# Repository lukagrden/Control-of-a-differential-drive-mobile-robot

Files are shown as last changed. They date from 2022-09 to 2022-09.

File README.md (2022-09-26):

# Upravljanjem mobilnim robotom na diferencijalni pogon - završni rad

## SAŽETAK

Završni rad opisuje modifikaciju mobilnog robota Pioneer 2DX koji koristi diferencijalni sustav pogona. Robot je nadograđen s novim upravljačkim i pogonskim komponentama uz koje je izrađen upravljački algoritam niske razine s mogućnošću dvosmjerne komunikacije s nadređenim upravljačkim računalima. U sklopu zadatka projektiran je regulator brzine vrtnje elektromotora čije su performanse ispitane odzivima na različite pobudne funkcije. Nadalje, primjenom jednadžbi direktne kinematike podređeni upravljački sustav vrši izračun referenci brzine vrtnje kotača u odnosu na željene translacijske i rotacijske brzine, dok se jednadžbama direktne kinematike tada preko enkodera estimiraju realne brzine robota. Serijska komunikacija s nadređenim računalom izvedena je pomoću robotskog operativnog sustava (eng. Robot Operating System – ROS) primjenom paketa „rosserial“. Dodatno, rad obuhvaća konstruiranje i izradu adaptera novih pogonskih motora tehnologijom 3D ispisa, uz koje je također prikazana shema spajanja upravljačkih komponenti te je izrađena prototipna pločica.

Sva dokumentacija koja se tiče upravljačkog programa s modoficiranim knjižnicama, nalazi se u završnom radu (Grden_2022_zavrsni_preddiplomski.pdf). Uz to na repozitoriju su dodane
step. datoteke modeliranih dijelovima zajedno s upravljačkim kodom mobilnog robota.

 

# Control of a differential drive mobile robot - final paper

## SUMMARY

The final paper describes the modification of the Pioneer 2DX mobile robot that uses a differential drive system. The robot was upgraded with new control and drive components, along with which a low-level control algorithm was created with the possibility of two-way communication with  a high-level controller. As part of the task, an electric motor rotation speed regulator was designed, whose performance was tested by responses to different input signals. Furthermore, by applying the equations of direct kinematics, the low-level control system calculates the reference speed of the wheels in relation to the desired translational and rotational speeds, while the equations of direct kinematics are then used to estimate the real speeds of the robot through the motor encoder. Serial communication with the high-level controller is performed with the robot operating system (Robot Operating System - ROS) using the "rosserial" package. In addition, the work includes constructing and manufacturing of adapters for new drive motors using 3D printing technology. Along with that, with  given connection scheme, the prototype circuit board is crated.

All documentation regarding control algorithm with modified libaries is included in the final paper (Grden_2022_zavrsni_preddiplomski.pdf). In addition, step. files of modeled parts together with the control code of the mobile robot are added to the repository.



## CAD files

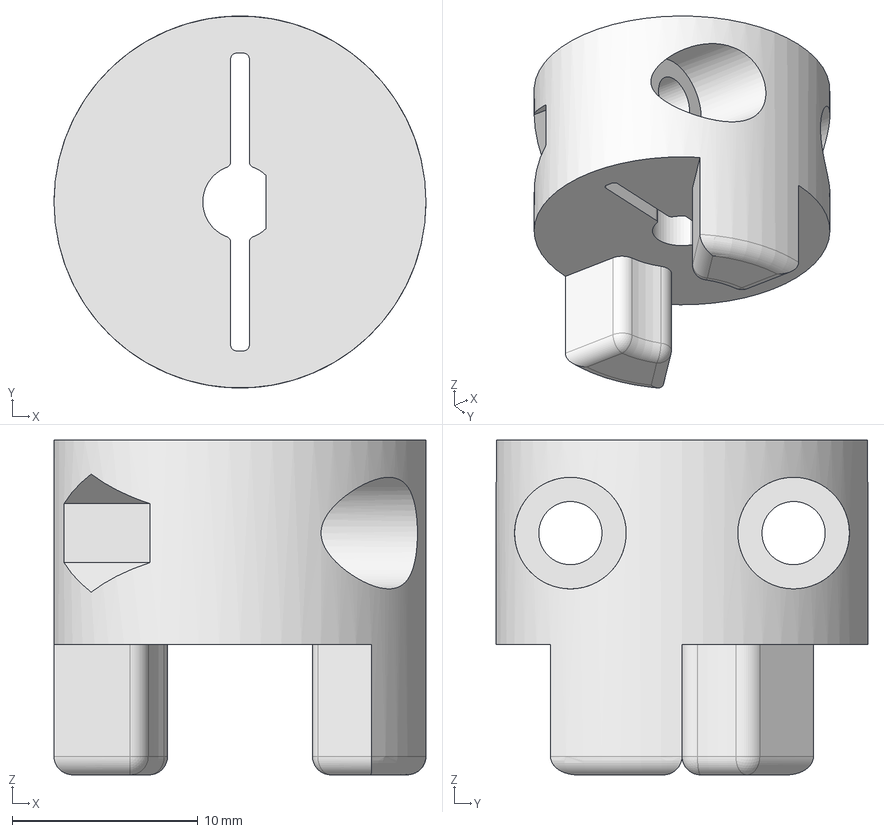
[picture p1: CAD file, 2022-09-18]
CAD/STEP datoteke ne standardnih dijelova/Segment spojke B MRP-02-01.stp
20.0 x 20.0 x 18.0 mm

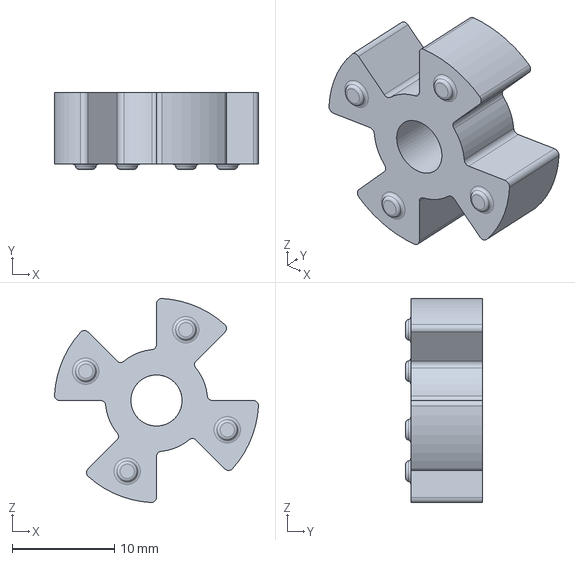
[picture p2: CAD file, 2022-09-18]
CAD/STEP datoteke ne standardnih dijelova/Elastični umetak MRP-02-02.stp
20.0 x 7.50 x 20.0 mm

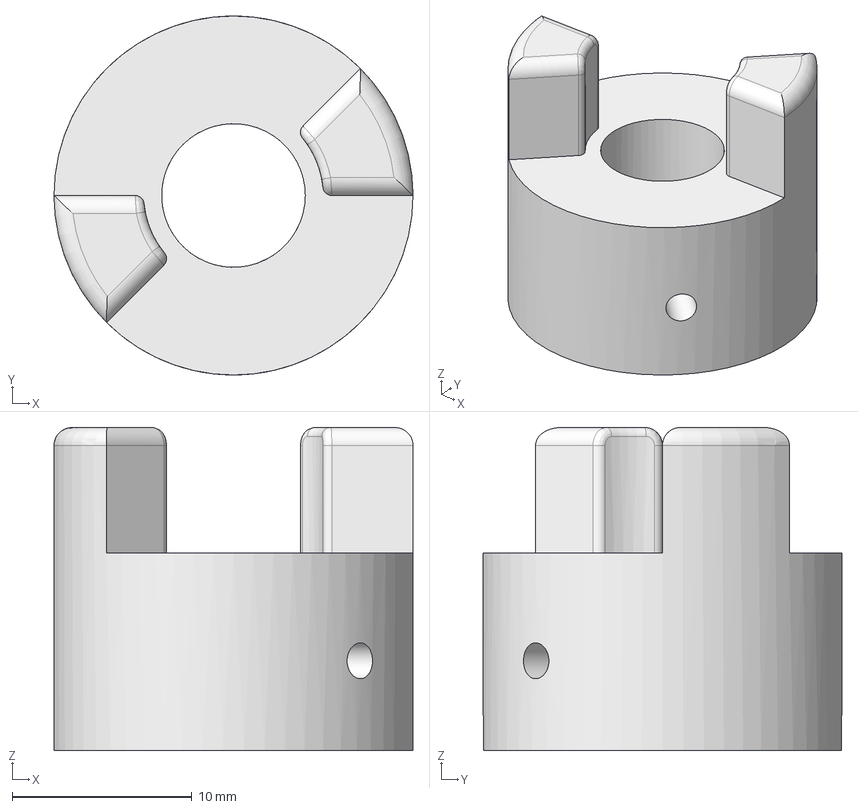
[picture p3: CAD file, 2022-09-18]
CAD/STEP datoteke ne standardnih dijelova/Segment spojke A MPR-02-03.stp
20.0 x 20.0 x 18.0 mm

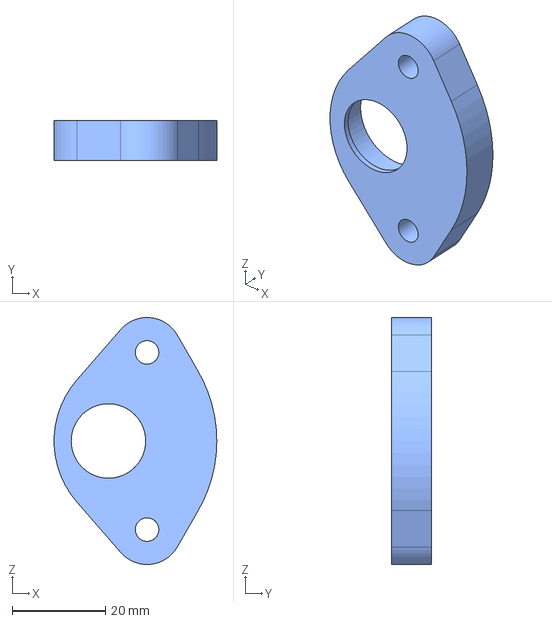
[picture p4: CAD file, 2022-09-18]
CAD/STEP datoteke ne standardnih dijelova/Nosač ležaja A MRP-01-04.stp
35.0 x 8.50 x 53.1 mm

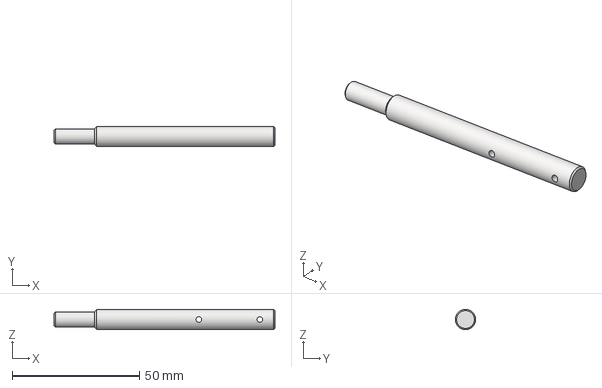
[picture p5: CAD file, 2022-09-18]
CAD/STEP datoteke ne standardnih dijelova/Vratilo kotača MRP-01-02.stp
87.0 x 8.00 x 8.00 mm

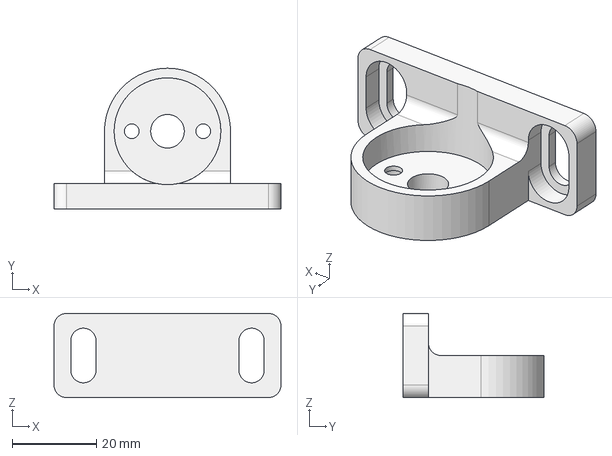
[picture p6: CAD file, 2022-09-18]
CAD/STEP datoteke ne standardnih dijelova/Nosač motora MRP-01-07.stp
54.0 x 33.5 x 20.0 mm

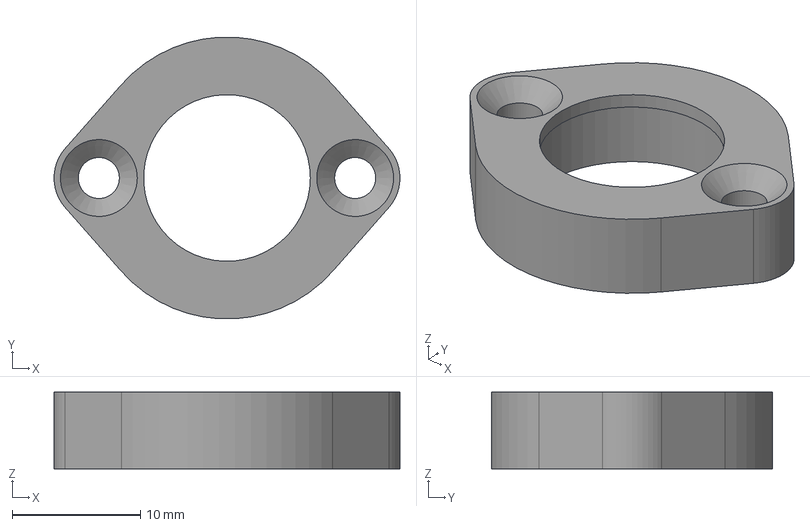
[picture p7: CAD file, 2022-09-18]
CAD/STEP datoteke ne standardnih dijelova/Nosač ležaja B MRP-01-08.stp
27.0 x 22.0 x 6.00 mm

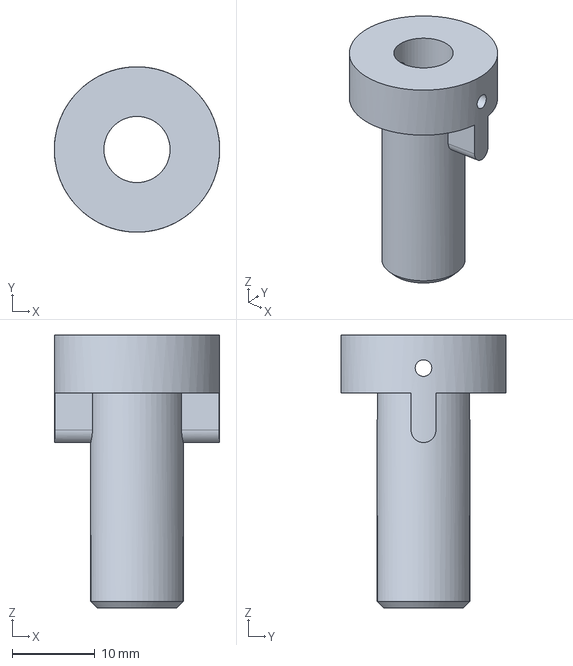
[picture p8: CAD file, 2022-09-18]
CAD/STEP datoteke ne standardnih dijelova/Adapter kotača MRP-01-03.stp
20.0 x 20.0 x 33.0 mm

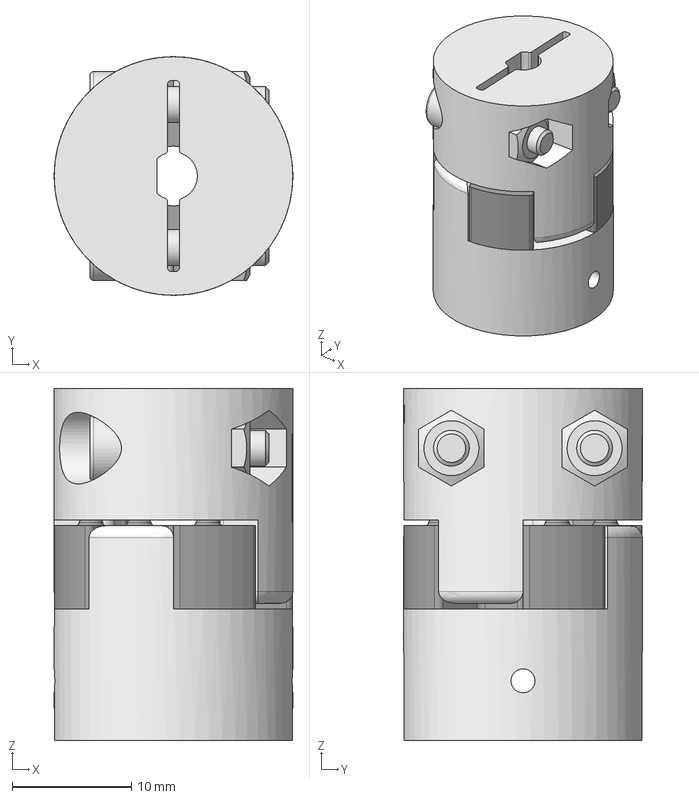
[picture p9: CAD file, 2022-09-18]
CAD/STEP datoteke ne standardnih dijelova/Spojka motora MRP-02-00.stp
20.0 x 20.0 x 29.5 mm
Spojka motora_4
Spojka motora_8_rev2
Kriz
DIN 555-5 - M3 x 2
DIN 912 - M3 x 12 x 2

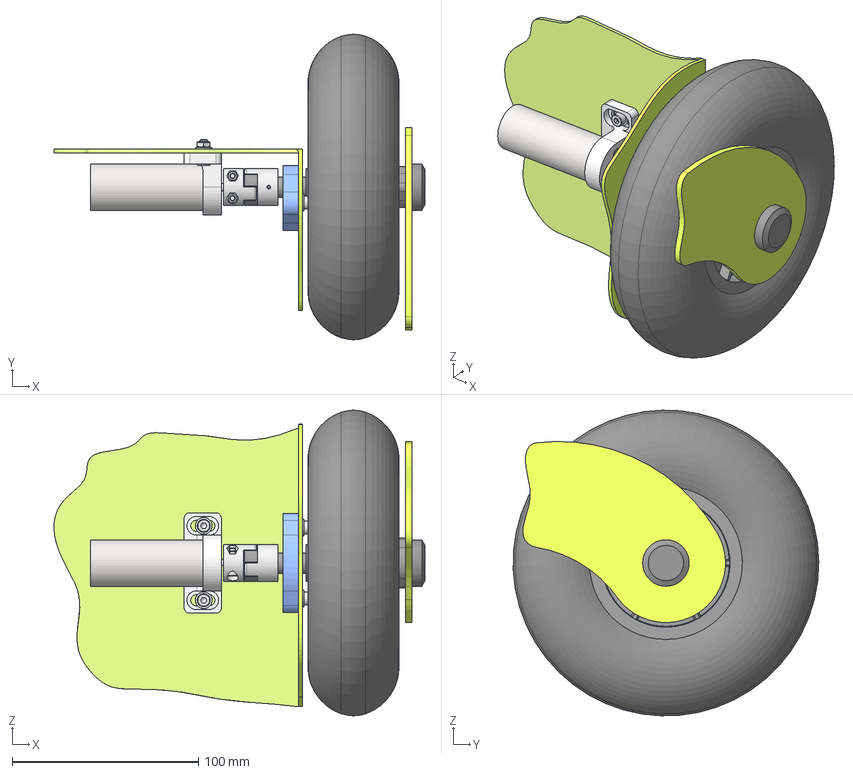
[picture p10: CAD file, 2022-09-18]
CAD/STEP datoteke ne standardnih dijelova/Pogonski sustav robota MRP-01-00.stp
199.4 x 164.3 x 164.3 mm
Kotač1
Kotač2
Guma
Vratilo
Spojka_kotača_novo
Lim
Motornovi
DIN 625 SKF - SKF 619/8
ISO 8752 - 2 x 20 x 2
Kucistelezaja_novo
Osigurac_lezaja_novo
Odstojnik_novo
Nosač_motora_novo
DIN 912 - M3 x 6 x 2
Nosač_zakrivljeni
Spojka motora_4
Spojka motora_8_rev2
Kriz
DIN 555-5 - M3 x 2
DIN 912 - M3 x 12 x 2
DIN 625 T1 - 619/6 - 6 x 15 x 5
DIN 555-5 - M8
Nosač_ležaja
Odstojnik_novo_3,7
DIN 433 - 6,4
Poklopac
DIN 7991 - M3x12 x 2
Ugradbena matica M4x6x6 x 2
DIN 912 - M4 x 10 x 4
DIN 125 - A 4,3 x 6
DIN 934 - M4 x 2

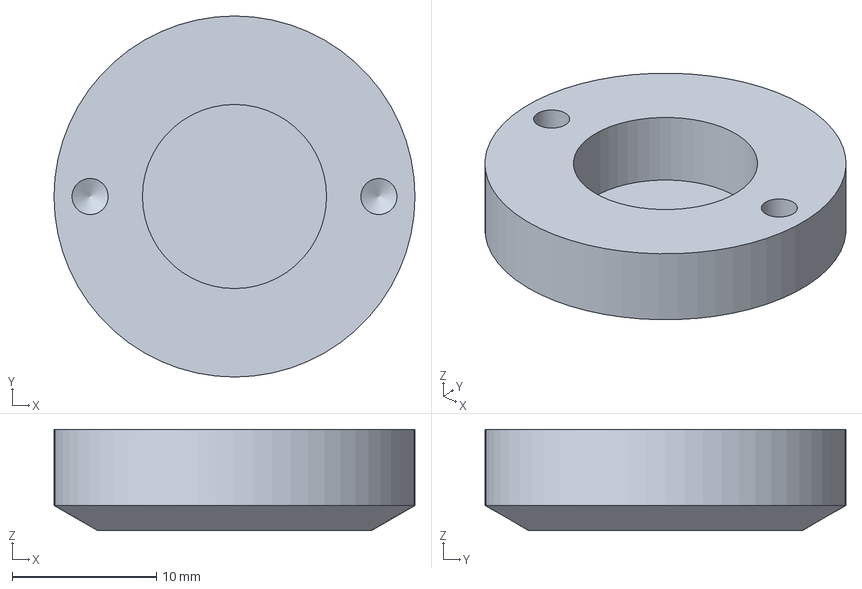
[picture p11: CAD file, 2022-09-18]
CAD/STEP datoteke ne standardnih dijelova/Poklopac MRP-01-01.stp
25.0 x 25.0 x 7.00 mm

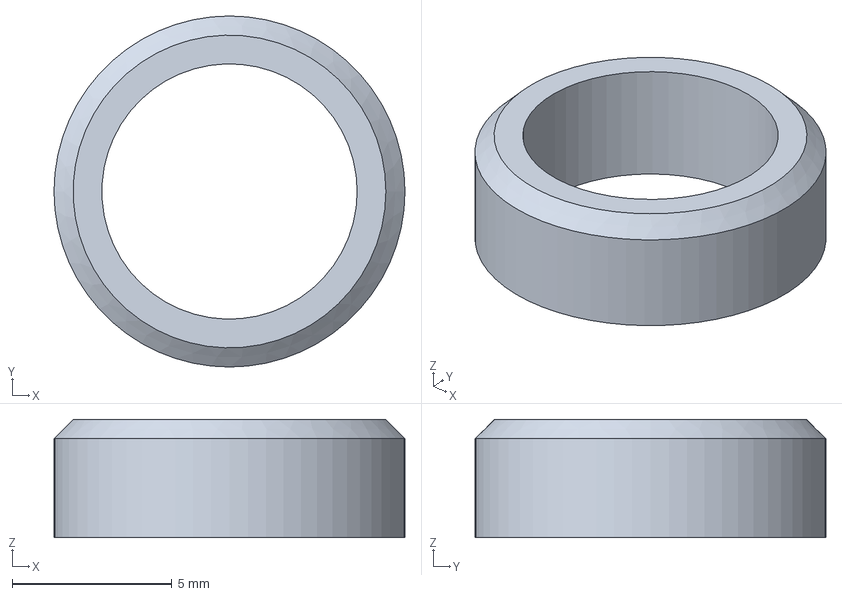
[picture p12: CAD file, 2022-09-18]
CAD/STEP datoteke ne standardnih dijelova/Odstojnik 3,7 MRP-01-09.stp
11.0 x 11.0 x 3.70 mm

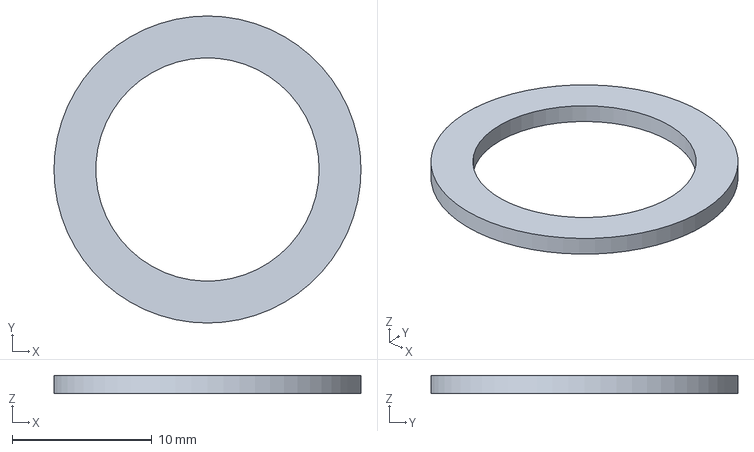
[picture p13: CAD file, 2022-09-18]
CAD/STEP datoteke ne standardnih dijelova/Osigurac ležaja MRP-01-05.stp
22.0 x 22.0 x 1.30 mm

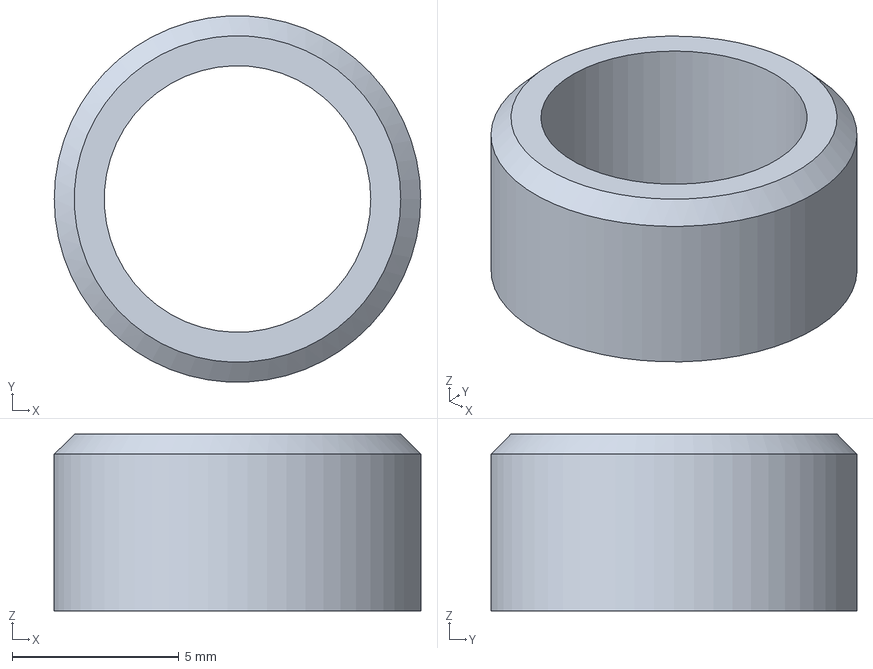
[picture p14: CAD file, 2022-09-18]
CAD/STEP datoteke ne standardnih dijelova/Odstojnik 5,1 MPR-01-06.stp
11.0 x 11.0 x 5.30 mm

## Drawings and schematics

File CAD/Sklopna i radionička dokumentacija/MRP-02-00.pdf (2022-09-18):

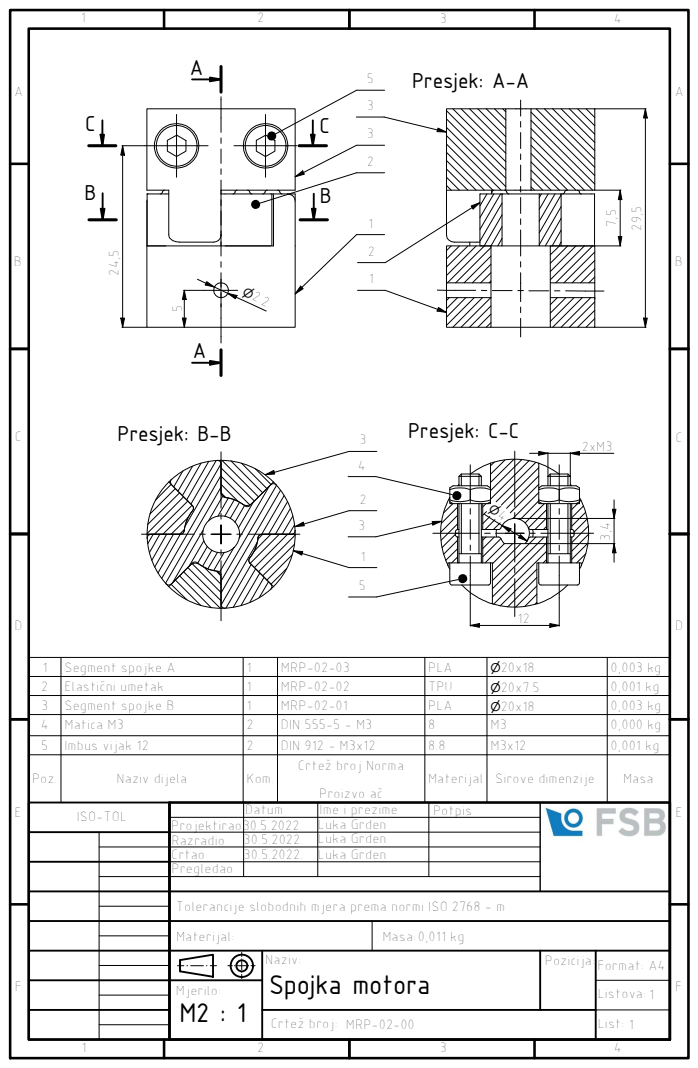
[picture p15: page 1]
Presjek: C-C; Presjek: A-A; Presjek: B-B

1 | Segment spojke A | 1 | MRP-02-03 | PLA | 20x18 | 0,003 kg
2 | Elastiáni umetak | 1 | MRP-02-02 | TPU | 20x7.5 | 0,001 kg
3 | Segment spojke B | 1 | MRP-02-01 | PLA | 20x18 | 0,003 kg
4 | Matica M3 | 2 | DIN 555-5 - M3 | 8 | M3 | 0,000 kg
5 | Imbus vijak 12 | 2 | DIN 912 - M3x12 | 8.8 | M3x12 | 0,001 kg
Poz. | Naziv dijela | Kom. | CrteË broj Norma Proizvo aá | Materijal | Sirove dimenzije | Masa

ISO-TOL | | Datum | Ime i prezime | Potpis

Projektirao | 30.5.2022. | Luka Grden
Razradio | 30.5.2022. | Luka Grden
Crtao | 30.5.2022. | Luka Grden
Pregledao

Tolerancije slobodnih mjera prema normi ISO 2768 - m

Materijal: | Masa: 0,011 kg

Naziv: Spojka motora | Pozicija: Format: | A4

Mjerilo: M2 : 1 | | | | Listova: 1
CrteË broj: MRP-02-00 | | 1 List:

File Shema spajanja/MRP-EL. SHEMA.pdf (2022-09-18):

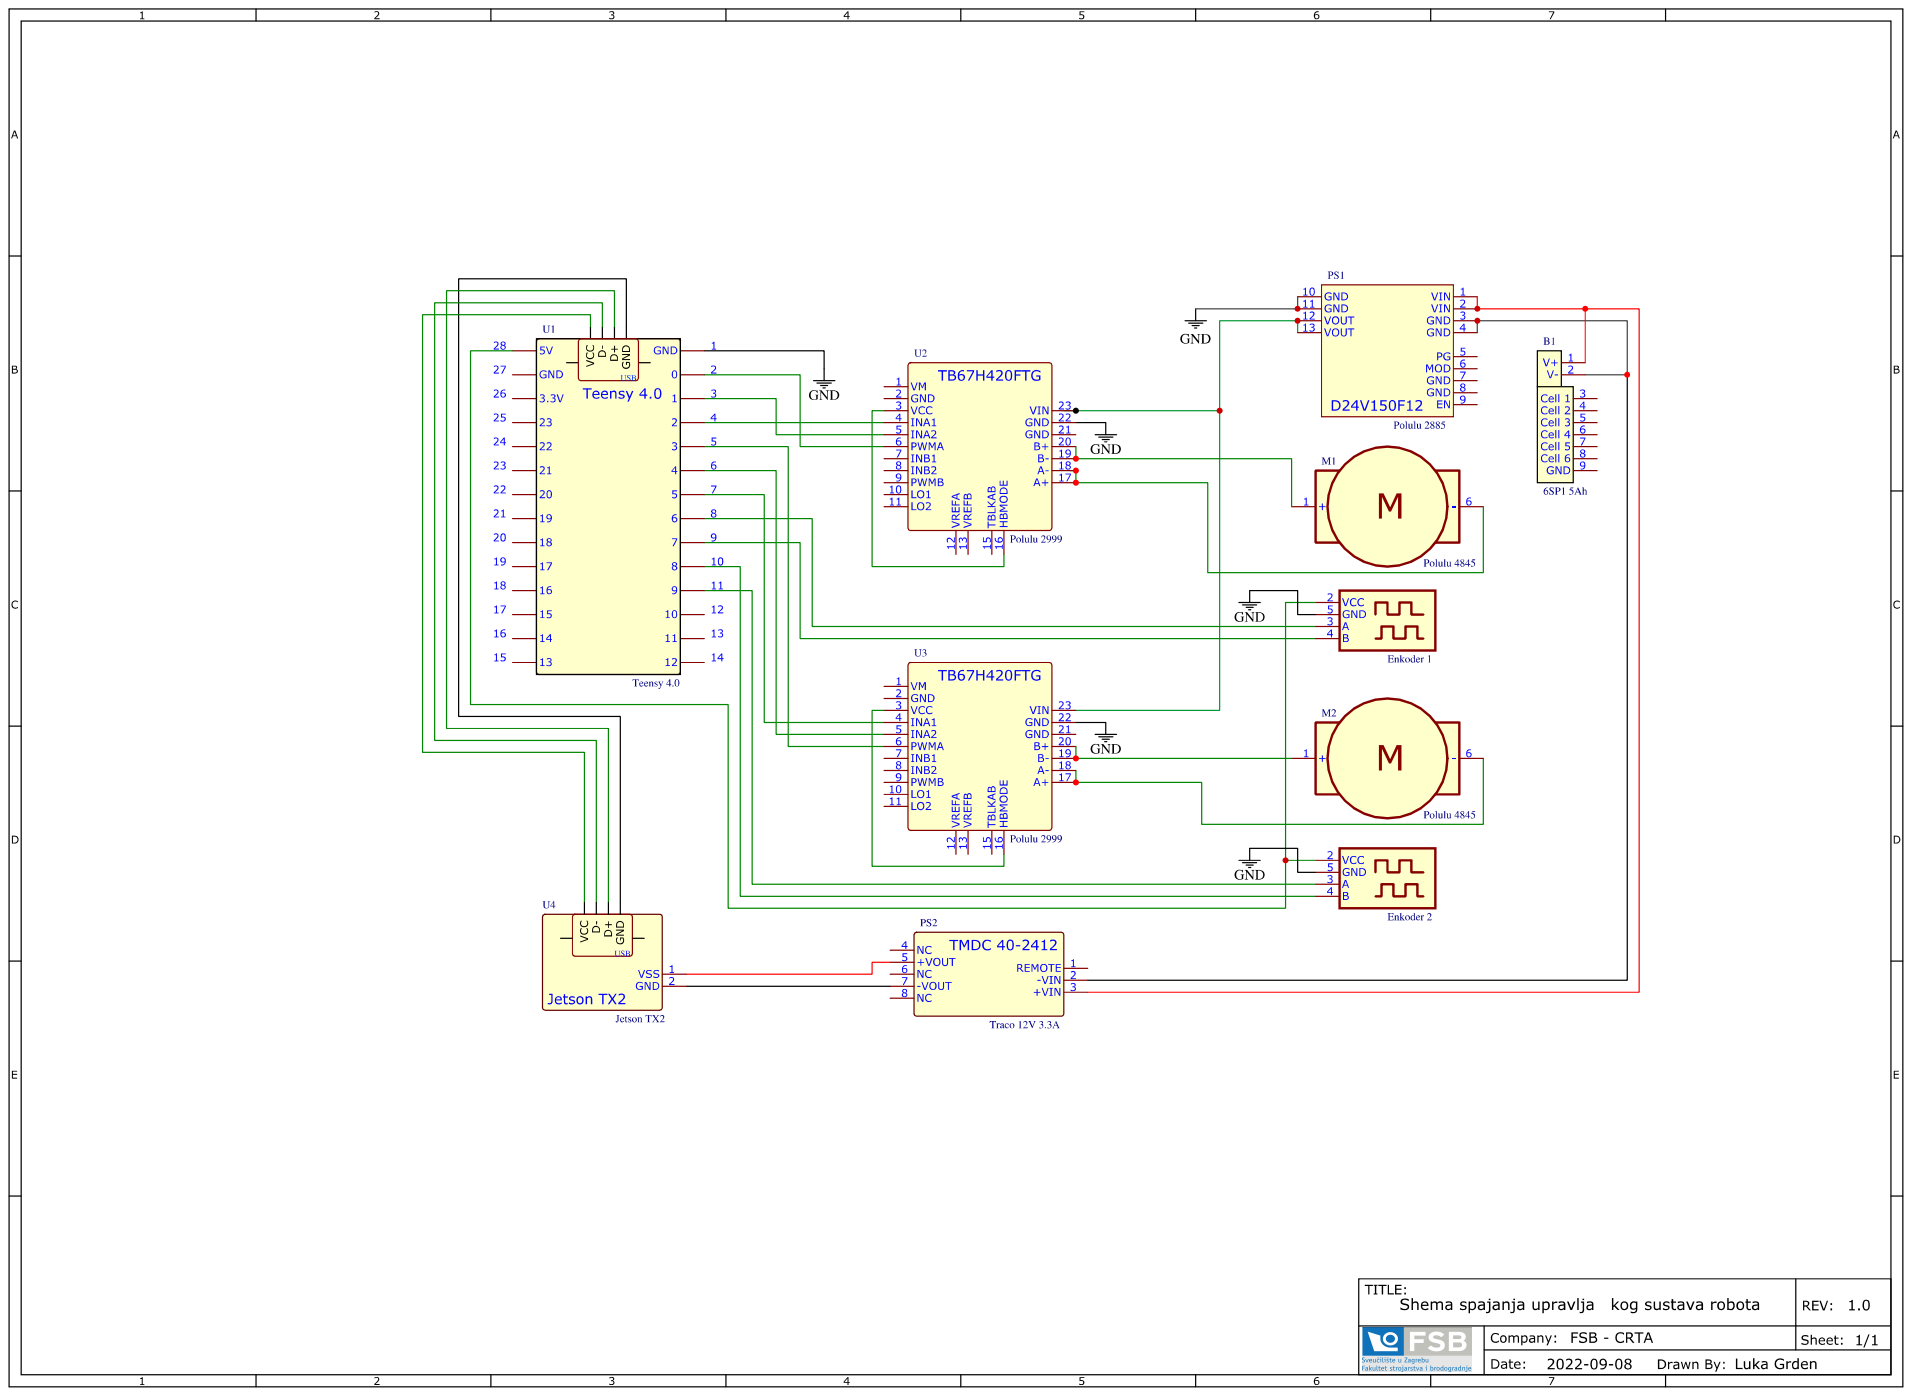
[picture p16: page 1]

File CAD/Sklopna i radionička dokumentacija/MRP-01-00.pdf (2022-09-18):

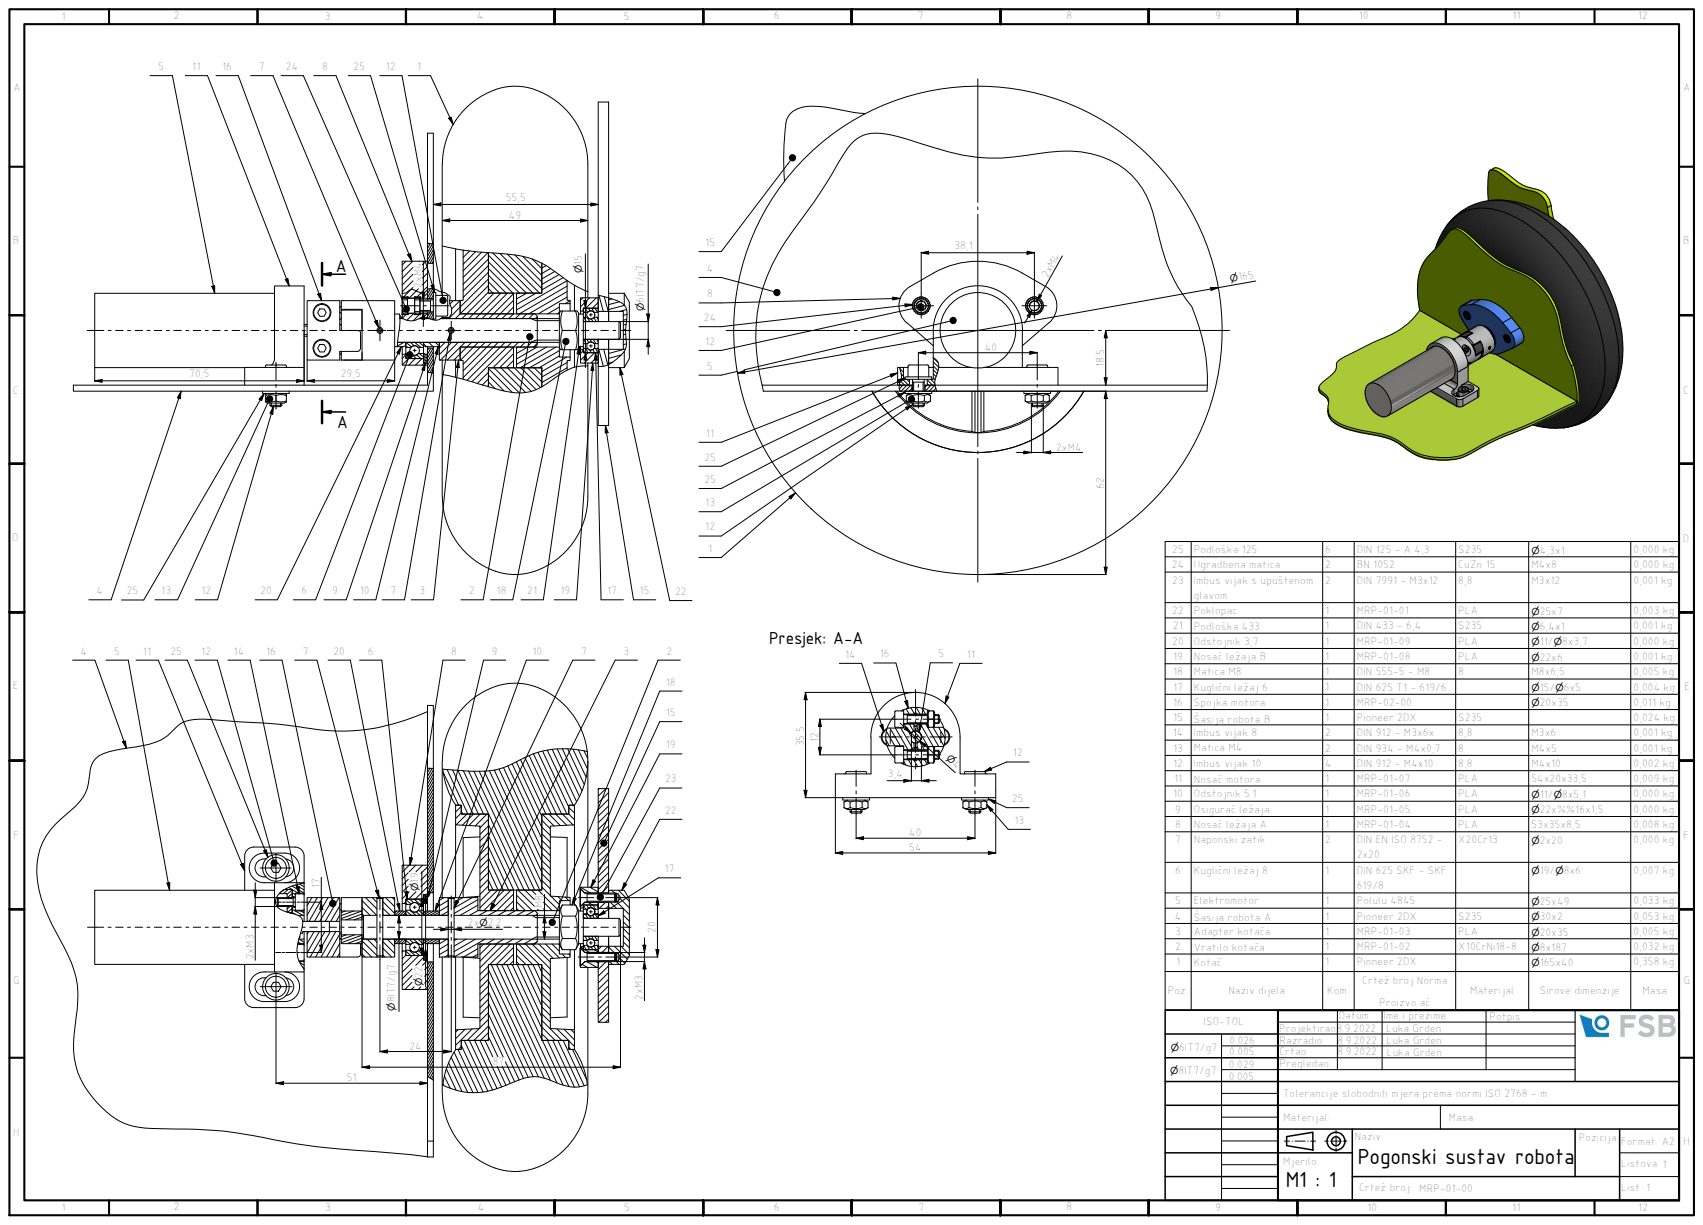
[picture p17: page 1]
rilo: Toleran; a: Naziv:

2 5 | P o dlo Ñ k a 1 2 5 | 6 | DIN 1 2 5 -A 4,3 | S 2 3 5 |  4,3 x 1 | 0,0 0 0 k g
2 4 | U g r a d b e n a m a tic a | 2 | B N 1 0 5 2 | C u Z n 1 5 | M 4 x 8 | 0,0 0 0 k
2 3 | | 2 | DIN 7991 - M3x12 | 8,8 | M3x12 | 0,001 kg glavom g Imbus vijak s upuÑtenom

2 2 | P o klo p a c | 1 | M R P -0 1 -0 1 | P L A |  2 5 x 7 | 0,0 0 3 k g
2 1 | Ñ P o dlo k a 4 3 3 | 1 | DIN 4 3 3 -6,4 | S 2 3 5 |  6,4 x 1 | 0,0 0 1 k g
2 0 | O d s t o j nik 3,7 | 1 | M R P -0 1 -0 9 | P L A |  1 1 /  8 x 3,7 | 0,0 0 0 k g

1 9 | N o s a á le Ë a j a B | 1 | M R P -0 1 -0 8 | P L A |  2 2 x 6 | 0,0 0 1 k g
1 8 | M a tic a M 8 | 1 | DIN 5 5 5 -5 -M 8 | 8 | M 8 x 6,5 | 0,0 0 5 k g
1 7 | K u gliá ni le Ë a j 6 | 1 | DIN 6 2 5 T 1 -6 1 9 / 6 | |   1 5 / 6 x 5 | 0,0 0 4 k g
1 6 | S p o j k a m o t o r a | 1 | M R P -0 2 -0 0 | |  2 0 x 3 5 | 0,0 1 1 k g
1 5 | Ò a sij a r o b o t a B | 1 | Pio n e e r 2 D X | S 2 3 5 | | 0,0 2 4 k g
1 4 | Im b u s vij a k 8 | 2 | DIN 9 1 2 -M 3 x 6 x | 8,8 | M 3 x 6 | 0,0 0 1 k g
1 3 | M a tic a M 4 | 2 | DIN 9 3 4 -M 4 x 0,7 | 8 | M 4 x 5 | 0,0 0 1 k g
1 2 | Im b u s vij a k 1 0 | 4 | DIN 9 1 2 -M 4 x 1 0 | 8,8 | M 4 x 1 0 | 0,0 0 2 k g
1 1 | N o s a á m o t o r a | 1 | M R P -0 1 -0 7 | P L A | 5 4 x 2 0 x 3 3,5 | 0,0 0 9 k g
1 0 | O d s t o j nik 5.1 | 1 | M R P -0 1 -0 6 | P L A |   1 1 / 8 x 5,1 | 0,0 0 0 k g
9 | O sig u r a á le Ë a j a | 1 | M R P -0 1 -0 5 | P L A |  2 2 x % % 1 6 x 1,5 | 0,0 0 0 k g
8 | N o s a á le Ë a j a A | 1 | M R P -0 1 -0 4 | P L A | 5 3 x 3 5 x 8,5 | 0,0 0 8 k g
7 | N a p o n s ki z a tik | 2 | DIN E N IS O 8 7 5 2 -2 x 2 0 | X 2 0 C r 1 3 |  2 x 2 0 | 0,0 0 0 k g

6 | K u gliá ni le Ë a j 8 | 1 | DIN 6 2 5 S K F -S K F 6 1 9 / 8 | |  1 9 /  8 x 6 | 0,0 0 7 k g

5 | Ele k t r o m o t o r | 1 | P olulu 4 8 4 5 | |  2 5 x 4 9 | 0,0 3 3 k g
4 | Ò a sij a r o b o t a A | 1 | Pio n e e r 2 D X | S 2 3 5 |  3 0 x 2 | 0,0 5 3 k g
3 | A d a p t e r k o t a á a | 1 | M R P -0 1 -0 3 | P L A |  2 0 x 3 5 | 0,0 0 5 k g
2 | V r a tilo k o t a á a | 1 | M R P -0 1 -0 2 | X 1 0 C r Ni1 8 -8 |  8 x 1 8 7 | 0,0 3 2 k g
1 | K o t a á | 1 | Pio n e e r 2 D X | |  1 6 5 x 4 0 | 0,3 5 8 k g
P o z. N | a ziv dij ela | K o | C r t e Ë b r o j N o r m a P r oiz v o a á | M a t e rij al | Sir o v e dim e n zij e | M a s a

D a t u m | Im e i p r e zim e | P o t pis

P r o j e k tir a o | 8.9.2 0 2 | n ISO-TOL u k a G r d e n
 6IT 7 / g 7 | 0.0 2 6 | R a z r a dio | 2. 8.9.2022. 8.9.2022. | L L u k a G r d e n

 8IT 7 / g 7 | 0.0 2 9 | P r e gle d a o

cij e slo b o d nih m j e r a p r e m a n o r mi IS O 2 7 6 8 -m

M a t e rij al: | M a s

o zicij a: F | List: Pogonski sustav robota MRP-01-00 o r m a t: Listova: CrteË broj: A 2

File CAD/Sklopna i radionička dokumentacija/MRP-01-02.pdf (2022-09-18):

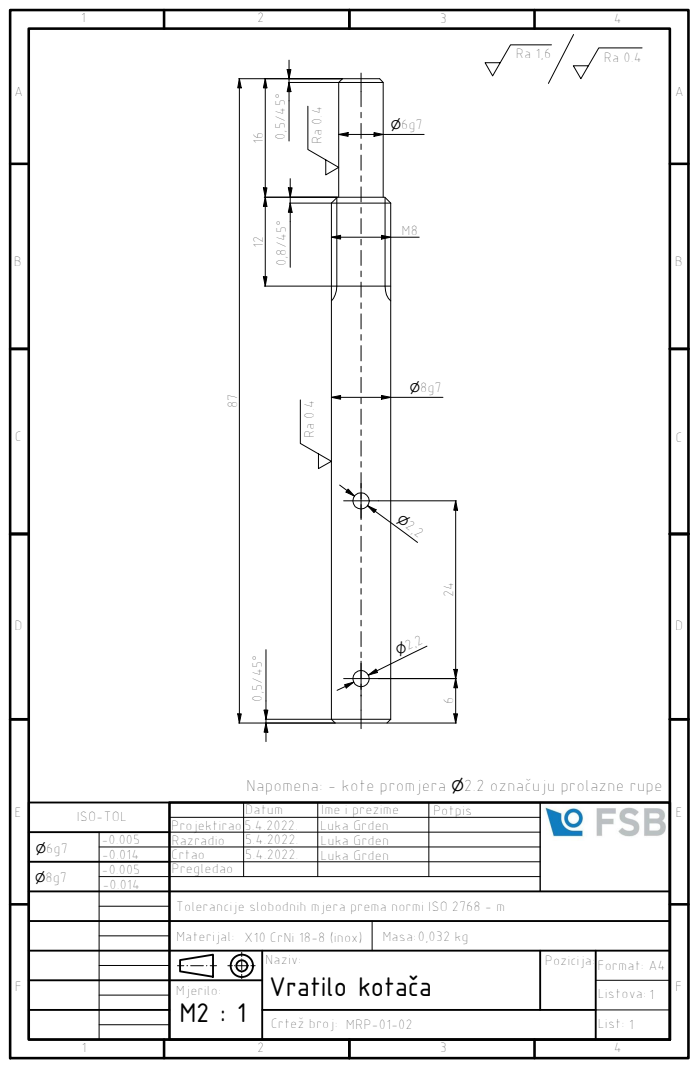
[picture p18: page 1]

Napomena: - kote promjera 2.2 oznaáuju prolazne rupe

ISO-TOL | | Datum | Ime i prezime | Potpis

Projektirao | 5.4.2022. | Luka Grden

6g7 | -0.005 | Razradio | 5.4.2022. | Luka Grden

-0.014 | Crtao | 5.4.2022. | Luka Grden

8g7 | -0.005 | Pregledao

Tolerancije slobodnih mjera prema normi ISO 2768 - m

Materijal: X10 CrNi 18-8 (inox) | Masa: 0,032 kg

Naziv: Vratilo kotaúa | Pozicija: Format: | A4

Mjerilo: M2 : 1 | | | | Listova: 1
CrteË broj: MRP-01-02 | | 1 List:

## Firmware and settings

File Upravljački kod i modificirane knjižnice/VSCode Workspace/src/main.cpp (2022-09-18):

#include <Arduino.h>
#include <elapsedMillis.h>
#include <ros.h>
#include <ros/time.h>
#include <geometry_msgs/Twist.h>
#include <tf/tf.h>
#include <tf/transform_broadcaster.h>
#include <nav_msgs/Odometry.h>
 

ros::NodeHandle nh;               // objekt za teensy čvor


// ********************** klasa regulatora************************

class RegulatorPI {
  private:
    float Pcw, Icw, Dcw;          // parametri regulatora
    float ewprev, ew;             // pogreska procesa i integracija pogreske procesa
    int PWMmax;                   // zasicenje regulatora
    int PWMmin;                   // mrtva zona motora
    float yP = 0;
    float yI = 0;
    float yD = 0;
    float yC = 0;
 
  public:
    RegulatorPI()
      : Pcw(0.0), Icw(0.0), Dcw(0.0), ewprev(0.0), PWMmax(255), PWMmin(55)  {}    // KONSTRUKTOR, početna inicializacija parametara

    void Parametri(float PcwIn, float IcwIn, float DcwIn) {                       // inicializacija parametara regulatora
      Pcw = PcwIn; Icw = IcwIn; Dcw = DcwIn;
    }

    // wC - upravljacki signal
    // wM - mjerena brzina
    // wR - referenca brzine
    // T  - period
    // PWM - PWM
    // direction - smijer

    void wC(float wM, float wR, float T, int &PWM, int &direction) {   // upravljacki signal regulatora (& - referenca memorijske lokacije)

      ew = wR - wM;
      //ewinteg = ewinteg + ew*T;          // integriranje greske, implicito
      yP = Pcw*ew;                         // proporcionalno djelovanje
      yI = yI+Icw*ew*T;                    // integralno djelovanje
      yD = Dcw*(ew-ewprev)/T;              // derivacijsko djelovanje
      yC = yP + yI + yD;                   // izlazni signal regulatora
      ewprev = ew;              
      
      PWM = (int) fabs(yC);                // upravljacki PWM signal zaokruzen na abs int
      if( PWM > PWMmax ) {                 // max PWM signal je 255
        PWM = PWMmax;
        yI = yC - yP - yD;                 // resetiranje integratora pri zasicenju
      }
      // else if( PWM>2 && PWM<PWMmin ) {    
      //   PWM = PWMmin;                   // kada padne ispod PWMmin onda pada u mrtvu zonu
      //   yI = yC - yP;                   // resetiranje integratora za mrtvu zonu
      //}
      
      direction = 1;                        // postavljeni smjer vrtnje motora
      if( yC < 0 ) {                        // ovisno vrijednosti regulatora
        direction = -1;                     // smjer se mjenja
      }
      else if( PWM<2 ) {                    // gašenje motora
        direction = 0;                
      }
  
//       Serial.print("e : ");
//       Serial.println(ew);
//       Serial.print("einteg : ");
//       Serial.println(ewinteg);
//       Serial.print("yC : ");
//       Serial.println(yC);
//       Serial.print("wR : ");
//       Serial.println(wR)

     }
};

// **************** varijable i pinovi *******************
#define nMotora  2                // broj motora
#define M1  0                     // motor 1
#define M2  1                     // motor 2
RegulatorPI regulatorW[nMotora];  // dvije (nMotora) instance regulatora

const int EncoderA[] = {6,9};     // encoderA motora 1 i 2
const int EncoderB[] = {7,8};     // encoderB    -||-
const int PWMpin[] = {0,3};       // PWMovi za motor 1 i 2
const int INA[] = {2,5};          // smjer + za motor 1 i 2
const int INB[] = {1,4};          // smjer -     -||-

volatile int ticks[] = {0,0};     // tickovi pojedinih enkodera u ReadEncoder()
long position[] = {0,0};          // suma tickova novo
long oldposition[] = {0,0};       // suma tickova staro
long dposition[] = {0,0};         // razlika tickova

double theta = 0;
double x = 0;
double y = 0;

unsigned long oldtime = 0;
elapsedMillis elapsedT;           // vrijeme u programu
unsigned int sampT=10;            // vrijeme uzorkovanja [mikrosekunde]

float wM[] = {0,0};               // mjerena brzina kotača    
float wMprev[] = {0,0};           // mjerena brtina kotača n-1 
float wMfilt[] = {0,0};           // filtritana brzina kotača

float wR[]={0,0};                 // referentna brzina kotača
float vrobota[]={0,0};            // linearna i kutna brzina robota
float vrobotaM[]={0,0,0};         // lineatna x,y i kutna mjerena brzina robota

unsigned int noCommMax = 800;      // maksimalan broj petlji u kojima komunikacija nije ostvarena ///////////////// stavi na 20
unsigned int noComm = 0;          // broj petlji u kojima komunikacija nije ostvarena

float r=0.165/2;                  // radius kotača
float L=0.380;                    // međuosovinski razmak

float rad = 0.0;                  // varijabla za sinusnu pobudu
unsigned long Tref;               // varijabla za početak pobude

// ********************* funkcije ***********************

void SetMotor(int INA, int INB, int PWMpin, int PWM, int direction)  {
// funkcija postavlja brzinu i smjer okretanja motora preko PWMa  
  analogWrite(PWMpin, PWM);            
  if(direction == 1) {                
    digitalWrite(INA, HIGH);       
    digitalWrite(INB, LOW);
  }
  else if(direction == -1) {
    digitalWrite(INA, LOW);
    digitalWrite(INB, HIGH);
  }
  else {
    digitalWrite(INA, HIGH);
    digitalWrite(INB, HIGH);
  }
}
 
template <int i>
void ReadEncoderA() {                        
  if(digitalRead(EncoderA[i])==HIGH) {  
    if(digitalRead(EncoderB[i])==HIGH) {
      ticks[i]++; }
    else {
      ticks[i]--; }                             
  }
  else {
    if(digitalRead(EncoderB[i])==HIGH) {
      ticks[i]--; }
    else {
      ticks[i]++; }
  }
}

template <int i>
void ReadEncoderB() {                        
  if(digitalRead(EncoderB[i])==HIGH) {  
    if(digitalRead(EncoderA[i])==HIGH) {
      ticks[i]--; }
    else {
      ticks[i]++; }                             
  }
  else {
    if(digitalRead(EncoderA[i])==HIGH) {
      ticks[i]++; }
    else {
      ticks[i]--; }
  }
}

void invKinematics(float Vtrans, float Wrot) {
// inverzna kinematika diferencialnog robota
  if (Vtrans>1) Vtrans=1;  // ogranicenje linearne brzine 
  if (Wrot>2) Wrot=2;      // ogranicenje kutne brzine
 
  wR[0]=-1/r*(Vtrans-L*Wrot)*60/(2*PI);
  wR[1]=1/r*(Vtrans+L*Wrot)*60/(2*PI);
}


void dirKinematics(float wM0, float wM1, double theta) {
// direktna kinematika diferencialnog robota
//  vrobotaM[0] = r*PI*(wM1-wM0)*cos(theta)/(60);
  vrobotaM[0] = r*PI*(wM1-wM0)/(60);
  vrobotaM[1] = r*PI*(wM1-wM0)*sin(theta)/(60);
  vrobotaM[2] = r*PI*(wM0+wM1)/(60*L);
}

void cmd_vel_Cb( const geometry_msgs::Twist& twist){   
// ROS subscriber na topic cmd_vel  
 noComm = 0;                    // resetiranje variable
 vrobota[0]= twist.linear.x;
 vrobota[1]= twist.angular.z;
}

ros::Subscriber<geometry_msgs::Twist> sub("cmd_vel", &cmd_vel_Cb );
tf::TransformBroadcaster broadcaster;
nav_msgs::Odometry odom_msg;
ros::Publisher odom_pub("odom", &odom_msg);
geometry_msgs::TransformStamped t; 

char base_link[] = "/base_link";
char odom[] = "/odom";

void setup() {
  
  nh.getHardware()->setBaud(115200);
  nh.initNode();                                // inicijalizacija komunikacije
  nh.subscribe(sub);
  nh.advertise(odom_pub);
  broadcaster.init(nh); 
  
  for (int i = 0; i < nMotora; i++ ) {          // deklaritanje pinova za nMotora
    pinMode(EncoderA[i], INPUT);        
    pinMode(EncoderB[i], INPUT);        
    pinMode(PWMpin[i], OUTPUT);
    pinMode(INA[i], OUTPUT);
    pinMode(INB[i], OUTPUT);
    analogWriteFrequency(PWMpin[i],40000);      // postavljanje frekvencije PWM signala
    regulatorW[i].Parametri(1.5,6,0);           // postavljanje parametara regulatora motora
  }
  attachInterrupt(digitalPinToInterrupt(EncoderA[M1]), ReadEncoderA<M1>, CHANGE);   // interupt za ReadEncoderA, kanal A M1
  attachInterrupt(digitalPinToInterrupt(EncoderB[M1]), ReadEncoderB<M1>, CHANGE);   // interupt za ReadEncoderB, kanal B M1
  attachInterrupt(digitalPinToInterrupt(EncoderA[M2]), ReadEncoderA<M2>, CHANGE);   // interupt za ReadEncoderA, kanal A M2
  attachInterrupt(digitalPinToInterrupt(EncoderB[M2]), ReadEncoderB<M2>, CHANGE);   // interupt za ReadEncoderB, kanal B M2
  }
    
void loop() {
  nh.spinOnce();                                 // pokretanje ROS čvorova za komunikaciju
  invKinematics(vrobota[0],vrobota[1]);          // postavljanje referenci kotača 
   
  if (elapsedT >= sampT) {                       // period uzorkovanja
    noInterrupts();                              // gasenje interupta za sigurno očitanje pozicije
    for(int j = 0; j < nMotora; j++){
      position[j] = ticks[j];                    // ocitanje pozicija obaju motora u vidu tickova
    }
    interrupts();
    float T = elapsedT/(1.0e3);                  // T [s]
    
    for(int i = 0; i < nMotora; i++){  
      dposition[i] = position[i]-oldposition[i];
      wM[i]=(dposition[i]*60)/(T*46.8512*12*4);                  // izracun brzine motora [RPM]
      oldposition[i]=position[i];
      wMprev[i]=wM[i];
      wMfilt[i]=0.7265*wMfilt[i]+0.1367*wM[i]+0.1367*wMprev[i];  // butterworth filter cutoff na 5Hz
    }

    for (int k = 0; k < nMotora; k++){                           // izlaz regulatora
      int PWM, direction;
      if ( noComm>=noCommMax ) {
        wR[k]=0;
        regulatorW[k].wC(wMfilt[k], wR[k], T, PWM, direction);
        SetMotor(INA[k], INB[k], PWMpin[k], PWM, direction);
      }
      regulatorW[k].wC(wMfilt[k], wR[k], T, PWM, direction);
      SetMotor(INA[k], INB[k], PWMpin[k], PWM, direction);
    }

    // direknta kinematika, integracija položaja
    theta += (2*r*PI*(dposition[0]+dposition[1]))/(46.8512*12*4*L);
    if (theta > PI) theta -= TWO_PI;
    if (theta < (-PI)) theta += TWO_PI;
    x += ((dposition[1]-dposition[0])*cos(theta))/2;
    y += ((dposition[1]-dposition[0])*sin(theta))/2;

    dirKinematics(wMfilt[0],wMfilt[1],theta);                  // direktna kinematika mobilnog robota

    t.header.frame_id = odom;
    t.child_frame_id = base_link;
    
    t.transform.translation.x = x/1000;   
    t.transform.translation.y = y/1000;
    t.transform.rotation.z = theta;
    t.transform.rotation = tf::createQuaternionFromYaw(theta);
    t.header.stamp = nh.now();
             
    broadcaster.sendTransform(t);

    nav_msgs::Odometry odom_msg;
    odom_msg.header.stamp = nh.now();
    odom_msg.header.frame_id = odom;
    
    odom_msg.pose.pose.position.x = x/1000;
    odom_msg.pose.pose.position.y = y/1000;
    odom_msg.pose.pose.position.z = 0.0;
    odom_msg.pose.pose.orientation = tf::createQuaternionFromYaw(theta);

    odom_msg.child_frame_id = base_link;
    odom_msg.twist.twist.linear.x = vrobotaM[0] ;       // forward linear velovity
    odom_msg.twist.twist.linear.y = vrobotaM[1];        // forward linear velovity                               
    odom_msg.twist.twist.angular.z = vrobotaM[2] ;      // anglular velocity
    odom_pub.publish(&odom_msg);
      
    noComm++;
    elapsedT=0;
  }
              
}









  
